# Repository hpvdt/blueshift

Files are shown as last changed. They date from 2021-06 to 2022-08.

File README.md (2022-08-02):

# Blueshift

Repository for our what would have been our 2020 ASME entry, Blueshift. Although the vehicle was never completed, the electronics were. The system is heavily based off of TITAN given they are both depend on a video system for the riders which is overlaid with vehicle data.

## Changes from TITAN

 However it has some changes from TITAN:
- Lighting hardware (and control) to meet road legality requirements
- Hardware was designed as an RPi HAT for a more compact system.
- Telemetry was operated by the microcontroller, not the RPi as on TITAN.
- Moved from a Python based overlay system to C based one to improve overlay update rate and prevent the overlay blacking out the video on occasion.

All systems were tested from home during the first set of lockdowns during COVID and were successful. So it is likely they would have worked just as well had the bike been built.

## Outcome

Work on this project ceased once the C-based overlay was working and telemetry was worked into it. Much of what was done for Blueshift will now go into improving TITAN for the future.

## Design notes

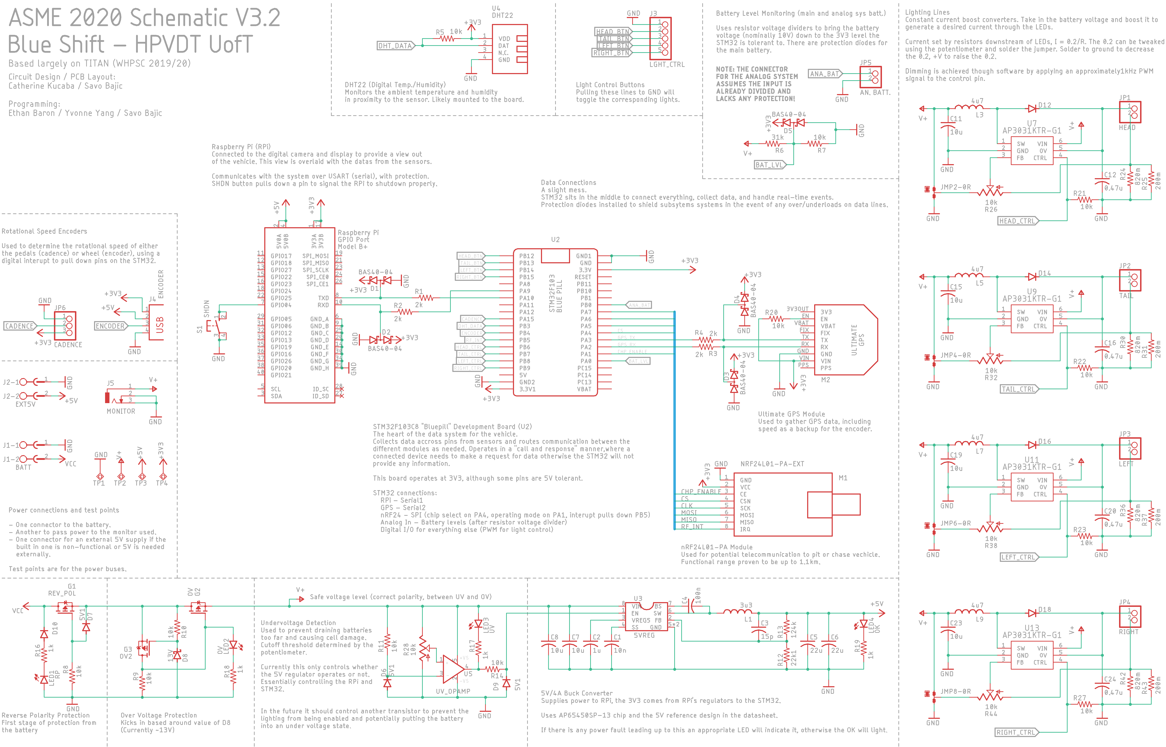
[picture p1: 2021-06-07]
Hardware/Schematic V3.2.png

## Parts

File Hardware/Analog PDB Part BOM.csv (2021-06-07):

Part | Value | Device | Package | Description
C1 | 10u | C-USC0603 | C0603 | CAPACITOR, American symbol
C2 | 4u7 | C-USC0603 | C0603 | CAPACITOR, American symbol
C3 | 2n2 | C-USC0603 | C0603 | CAPACITOR, American symbol
C4 | 10n | C-USC0603 | C0603 | CAPACITOR, American symbol
D1 | 0v2 | BOOSTDIODE | DO-214AB
H1 | MOUNT-HOLE3.3 | MOUNT-HOLE3.3 | 3,3 | MOUNTING HOLE with drill center marker
H2 | MOUNT-HOLE3.3 | MOUNT-HOLE3.3 | 3,3 | MOUNTING HOLE with drill center marker
L1 | 4u7 | SDEI054T | SDES053T | 4.7uH Inductor
R1 | 86k6 | R-US_R0402 | R0402 | RESISTOR, American symbol
R2 | 10k | R-US_R0402 | R0402 | RESISTOR, American symbol
R3 | 10k | R-US_R0402 | R0402 | RESISTOR, American symbol
R4 | 100k | R-US_R0402 | R0402 | RESISTOR, American symbol
R5 | 100k | R-US_R0402 | R0402 | RESISTOR, American symbol
U1 | MP3213DH | MP3213DH | 8-TSSOP | 3.5A Boost Converter Regulator
X1 | BATT | MST2V | MSTBV2 | PHOENIX
X2 | CAM1 | MSTBV2 | MSTBV2 | PHOENIX
X3 | CAM2 | MSTBV2 | MSTBV2 | PHOENIX
X4 | CAM3 | MSTBV2 | MSTBV2 | PHOENIX
X5 | DIS1 | MSTBV2 | MSTBV2 | PHOENIX
X6 | DIS2 | MSTBV2 | MSTBV2 | PHOENIX
X7 | DIS3 | MSTBV2 | MSTBV2 | PHOENIX

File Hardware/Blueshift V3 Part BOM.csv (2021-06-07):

Part | Value | Device | Package | Description
C1 | 10n | C-USC0402 | C0402 | CAPACITOR, American symbol
C2 | 1u | C-USC0402 | C0402 | CAPACITOR, American symbol
C3 | 15p | C-USC0402 | C0402 | CAPACITOR, American symbol
C4 | 100n | C-USC0402 | C0402 | CAPACITOR, American symbol
C5 | 22u | C-USC0805 | C0805 | CAPACITOR, American symbol
C6 | 22u | C-USC0805 | C0805 | CAPACITOR, American symbol
C7 | 10u | C-USC0805 | C0805 | CAPACITOR, American symbol
C8 | 10u | C-USC0805 | C0805 | CAPACITOR, American symbol
C11 | 10u | C-USC1206K | C1206K | CAPACITOR, American symbol
C12 | 0.47u | C-USC1206K | C1206K | CAPACITOR, American symbol
C15 | 10u | C-USC1206K | C1206K | CAPACITOR, American symbol
C16 | 0.47u | C-USC1206K | C1206K | CAPACITOR, American symbol
C19 | 10u | C-USC1206K | C1206K | CAPACITOR, American symbol
C20 | 0.47u | C-USC1206K | C1206K | CAPACITOR, American symbol
C23 | 10u | C-USC1206K | C1206K | CAPACITOR, American symbol
C24 | 0.47u | C-USC1206K | C1206K | CAPACITOR, American symbol
D1 | BAS40-04 | BAS40-04 | SOT23 | Silicon Schottky Diodes
D2 | BAS40-04 | BAS40-04 | SOT23 | Silicon Schottky Diodes
D3 | BAS40-04 | BAS40-04 | SOT23 | Silicon Schottky Diodes
D4 | BAS40-04 | BAS40-04 | SOT23 | Silicon Schottky Diodes
D5 | BAS40-04 | BAS40-04 | SOT23 | Silicon Schottky Diodes
D6 | 5V1 | DIODE-SOD323-R | SOD323-R | DIODE
D7 | 5V1 | DIODE-SOD323-R | SOD323-R | DIODE
D8 | 13V | BAS70 | SOT23 | Silicon Schottky Diodes
D9 | 5V1 | DIODE-SOD323-R | SOD323-R | DIODE
D10 |  | DIODE-SOD80C | SOD80C | DIODE
D12 |  | DIODE-DO-214AC | DO-214AC | DIODE
D14 |  | DIODE-DO-214AC | DO-214AC | DIODE
D16 |  | DIODE-DO-214AC | DO-214AC | DIODE
D18 |  | DIODE-DO-214AC | DO-214AC | DIODE
G1 | REV_POL | SI3493DDV-T1-GE3 | TSOP-6 | 20V P-CH MOSFET
G2 | OV | SI3493DDV-T1-GE3 | TSOP-6 | 20V P-CH MOSFET
G3 | OV2 | SI3493DDV-T1-GE3 | TSOP-6 | 20V P-CH MOSFET
J1 | BATT | MST2V | MSTBV2 | PHOENIX
J2 | EXT5V | MST2V | MSTBV2 | PHOENIX
J3 | LGHT_CTRL | PINHD-1X5 | 1X05 | PIN HEADER
J4 | ENCODER | PN87520 | PN87520 | BERG USB connector
J5 | MONITOR | DCJ0303 | DCJ0303 | DC POWER JACK
JMP2 | 0R-JUMPA | 0R-JUMPA | A0R-JMP | SMD 0R 0805 Jumper
JMP4 | 0R-JUMPA | 0R-JUMPA | A0R-JMP | SMD 0R 0805 Jumper
JMP6 | 0R-JUMPA | 0R-JUMPA | A0R-JMP | SMD 0R 0805 Jumper
JMP8 | 0R-JUMPA | 0R-JUMPA | A0R-JMP | SMD 0R 0805 Jumper
JP1 | HEAD | PINHD-1X2 | 1X02 | PIN HEADER
JP2 | TAIL | PINHD-1X2 | 1X02 | PIN HEADER
JP3 | LEFT | PINHD-1X2 | 1X02 | PIN HEADER
JP4 | RIGHT | PINHD-1X2 | 1X02 | PIN HEADER
JP5 | AN. BATT. | PINHD-1X2 | 1X02 | PIN HEADER
JP6 | CADENCE | PINHD-1X3 | 1X03 | PIN HEADER
L1 | 3u3 | SDES064T-3R3MS | SDES064T
L3 | 4u7 | NR6028NR6028 | INDDFN600X600X280-2N
L5 | 4u7 | NR6028NR6028 | INDDFN600X600X280-2N
L7 | 4u7 | NR6028NR6028 | INDDFN600X600X280-2N
L9 | 4u7 | NR6028NR6028 | INDDFN600X600X280-2N
LED1 | RP | LEDSML0805 | SML0805 | LED
LED2 | OV | LEDSML0805 | SML0805 | LED
LED3 | UV | LEDSML0805 | SML0805 | LED
LED4 | OK | LEDSML0805 | SML0805 | LED
M1 | NRF24L01-PA-EXT | WIRELESS-NRF24L01-PA-EXT | WIRELESS-NRF24L01-PA-EXT | 2.4 GHz Wireless Module based on NRF24L01 chip with preamplifier and external antenna
M2 | ULTIMATE-GPS | ULTIMATE-GPS | ULTIMATE_GPS
R1 | 2k | R-US_R0402 | R0402 | RESISTOR, American symbol
R2 | 2k | R-US_R0402 | R0402 | RESISTOR, American symbol
R3 | 2k | R-US_R0402 | R0402 | RESISTOR, American symbol
R4 | 2k | R-US_R0402 | R0402 | RESISTOR, American symbol
R5 | 10k | R-US_R0402 | R0402 | RESISTOR, American symbol
R6 | 31k | R-US_R0402 | R0402 | RESISTOR, American symbol
R7 | 10k | R-US_R0402 | R0402 | RESISTOR, American symbol
R8 | 10k | R-US_R0402 | R0402 | RESISTOR, American symbol
R9 | 10k | R-US_R0402 | R0402 | RESISTOR, American symbol
R10 | 10k | R-US_R0402 | R0402 | RESISTOR, American symbol
R11 | 10k | R-US_R0402 | R0402 | RESISTOR, American symbol
R12 | 22k1 | R-US_R0402 | R0402 | RESISTOR, American symbol
R13 | 124k | R-US_R0402 | R0402 | RESISTOR, American symbol
R14 | 10k | R-US_R0402 | R0402 | RESISTOR, American symbol
R16 | 1k | R-US_R0402 | R0402 | RESISTOR, American symbol
R17 | 1k | R-US_R0402 | R0402 | RESISTOR, American symbol
R18 | 1k | R-US_R0402 | R0402 | RESISTOR, American symbol
R19 | 1k | R-US_R0402 | R0402 | RESISTOR, American symbol
R20 | 10k | R-US_R0402 | R0402 | RESISTOR, American symbol
R21 | 10k | R-US_R0402 | R0402 | RESISTOR, American symbol
R22 | 10k | R-US_R0402 | R0402 | RESISTOR, American symbol
R23 | 10k | R-US_R0402 | R0402 | RESISTOR, American symbol
R24 | 820m | R-US_R0603 | R0603 | RESISTOR, American symbol
R25 | 200m | R-US_R0805 | R0805 | RESISTOR, American symbol
R26 | 10k | TRIM_US-RJ9W | RJ9W | POTENTIOMETER
R27 | 10k | R-US_R0402 | R0402 | RESISTOR, American symbol
R28 | 10k | TRIM_US-RJ9W | RJ9W | POTENTIOMETER
R30 | 820m | R-US_R0603 | R0603 | RESISTOR, American symbol
R31 | 200m | R-US_R0805 | R0805 | RESISTOR, American symbol
R32 | 10k | TRIM_US-RJ9W | RJ9W | POTENTIOMETER
R36 | 820m | R-US_R0603 | R0603 | RESISTOR, American symbol
R37 | 200m | R-US_R0805 | R0805 | RESISTOR, American symbol
R38 | 10k | TRIM_US-RJ9W | RJ9W | POTENTIOMETER
R42 | 820m | R-US_R0603 | R0603 | RESISTOR, American symbol
R43 | 200m | R-US_R0805 | R0805 | RESISTOR, American symbol
R44 | 10k | TRIM_US-RJ9W | RJ9W | POTENTIOMETER
S1 | SHDN | 10-XX | B3F-10XX | OMRON SWITCH
TP1 | TPSQTP20SQ | TPSQTP20SQ | TP20SQ | Test pad
TP2 | TPSQTP20R | TPSQTP20R | TP20R | Test pad
TP3 | TPSQTP20R | TPSQTP20R | TP20R | Test pad
TP4 | TPSQTP20R | TPSQTP20R | TP20R | Test pad
U1 | RASPI_HAT | RASPI_HAT | RASPI_BOARD_B+HAT_CF
U2 | BLUEPILL | BLUE_PILL | BLUE_PILL
U3 | 5VREG | AP65450SP-13 | SO-8EP | AP65450
U4 | DHT22 | TEMP-HUM-SENSOR-DHT22 | TEMP-HUM-SENSOR-DHT22 | DHT22 - digital humidity & temperature sensor
U5 | UV_OPAMP | TA75S558F,LF | SOT-753
U7 | AP3031KTR-G1 | AP3031KTR-G1 | SOT23-6 | AP3031 step-up LED driver chip for LEDs up to 1.4A
U9 | AP3031KTR-G1 | AP3031KTR-G1 | SOT23-6 | AP3031 step-up LED driver chip for LEDs up to 1.4A
U11 | AP3031KTR-G1 | AP3031KTR-G1 | SOT23-6 | AP3031 step-up LED driver chip for LEDs up to 1.4A
U13 | AP3031KTR-G1 | AP3031KTR-G1 | SOT23-6 | AP3031 step-up LED driver chip for LEDs up to 1.4A

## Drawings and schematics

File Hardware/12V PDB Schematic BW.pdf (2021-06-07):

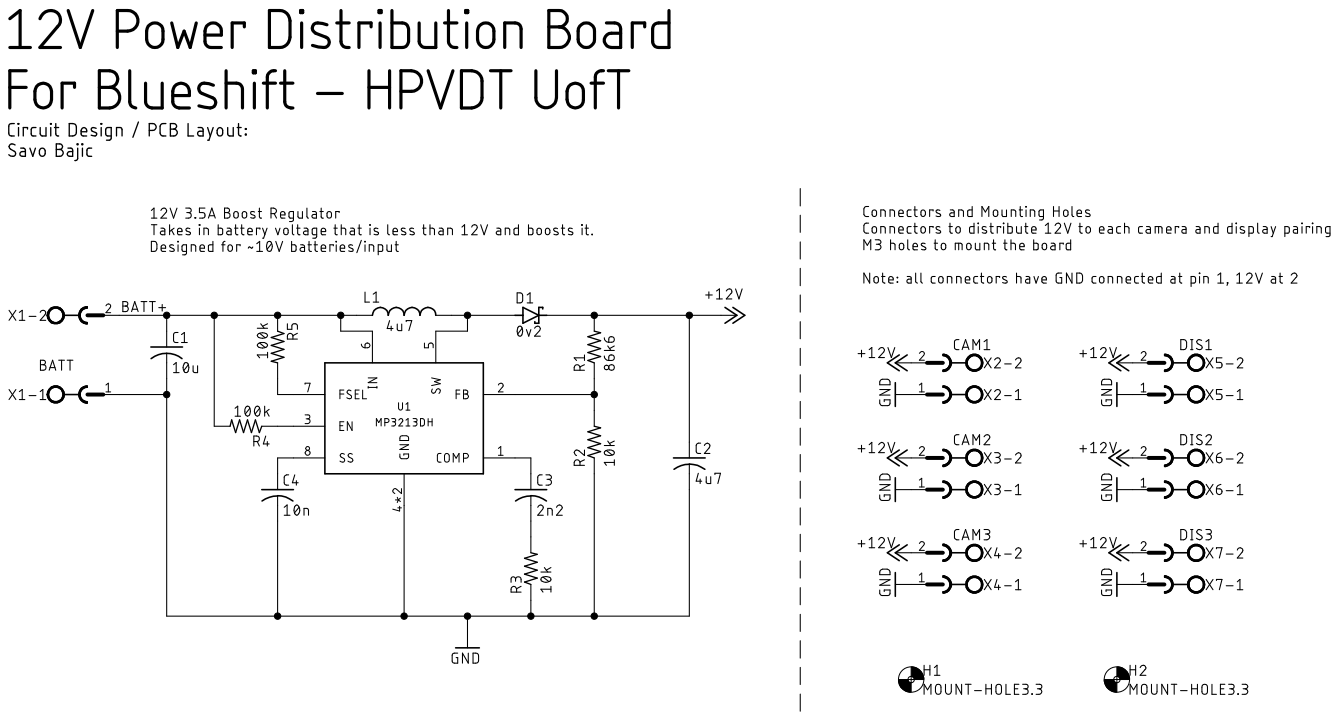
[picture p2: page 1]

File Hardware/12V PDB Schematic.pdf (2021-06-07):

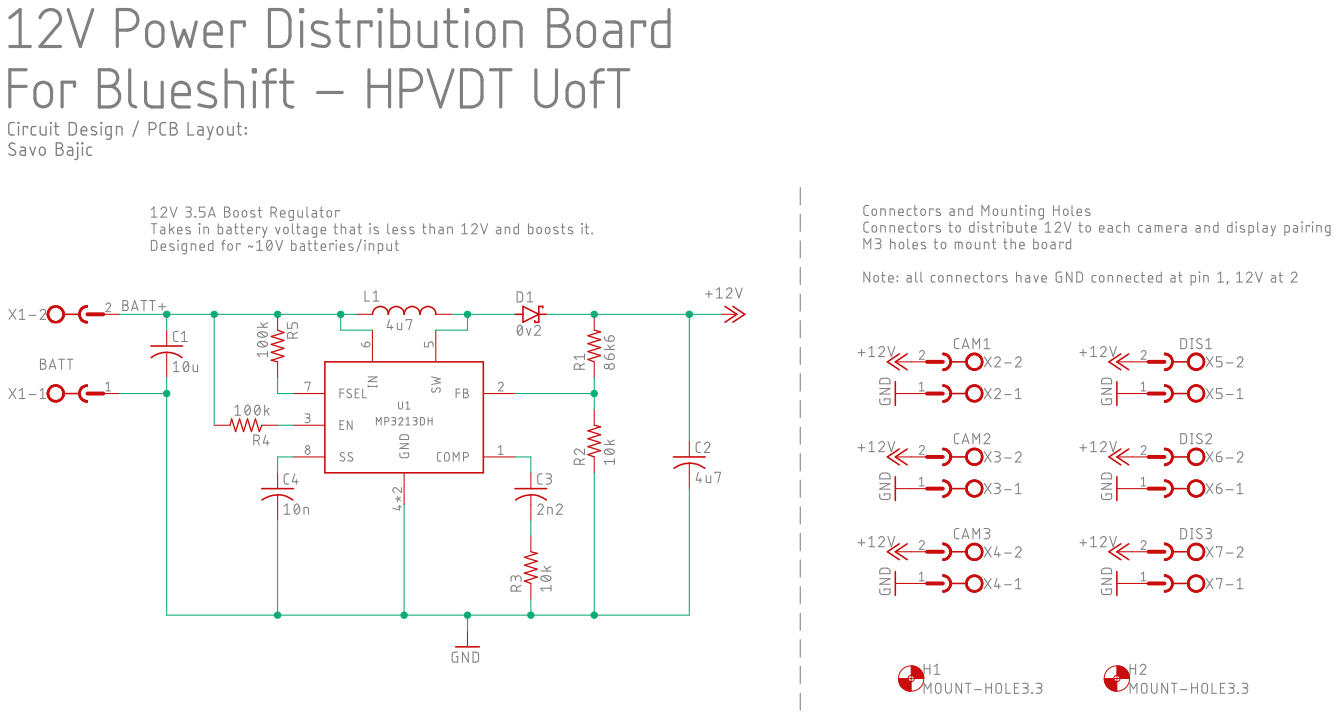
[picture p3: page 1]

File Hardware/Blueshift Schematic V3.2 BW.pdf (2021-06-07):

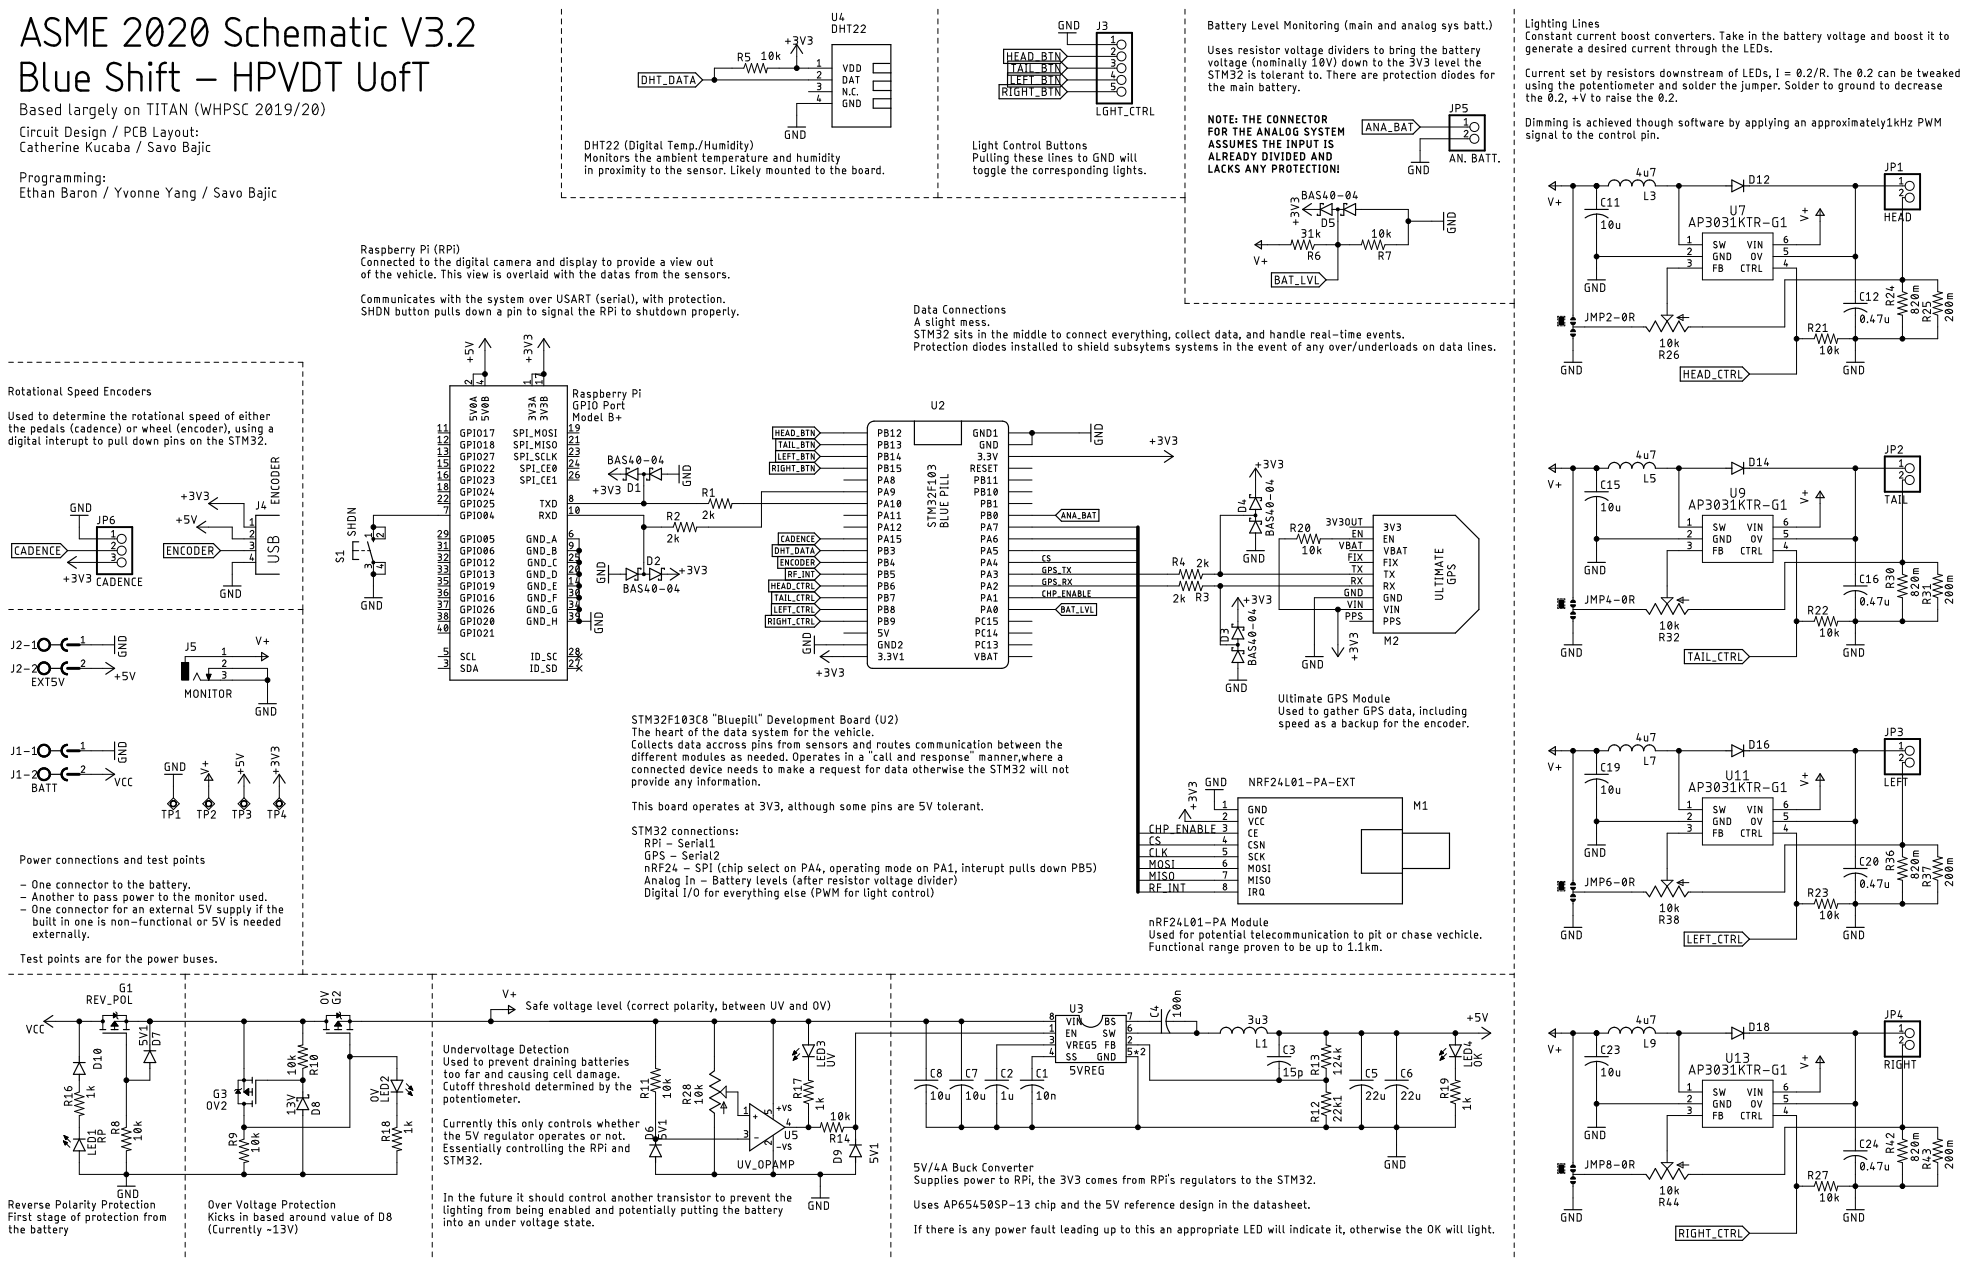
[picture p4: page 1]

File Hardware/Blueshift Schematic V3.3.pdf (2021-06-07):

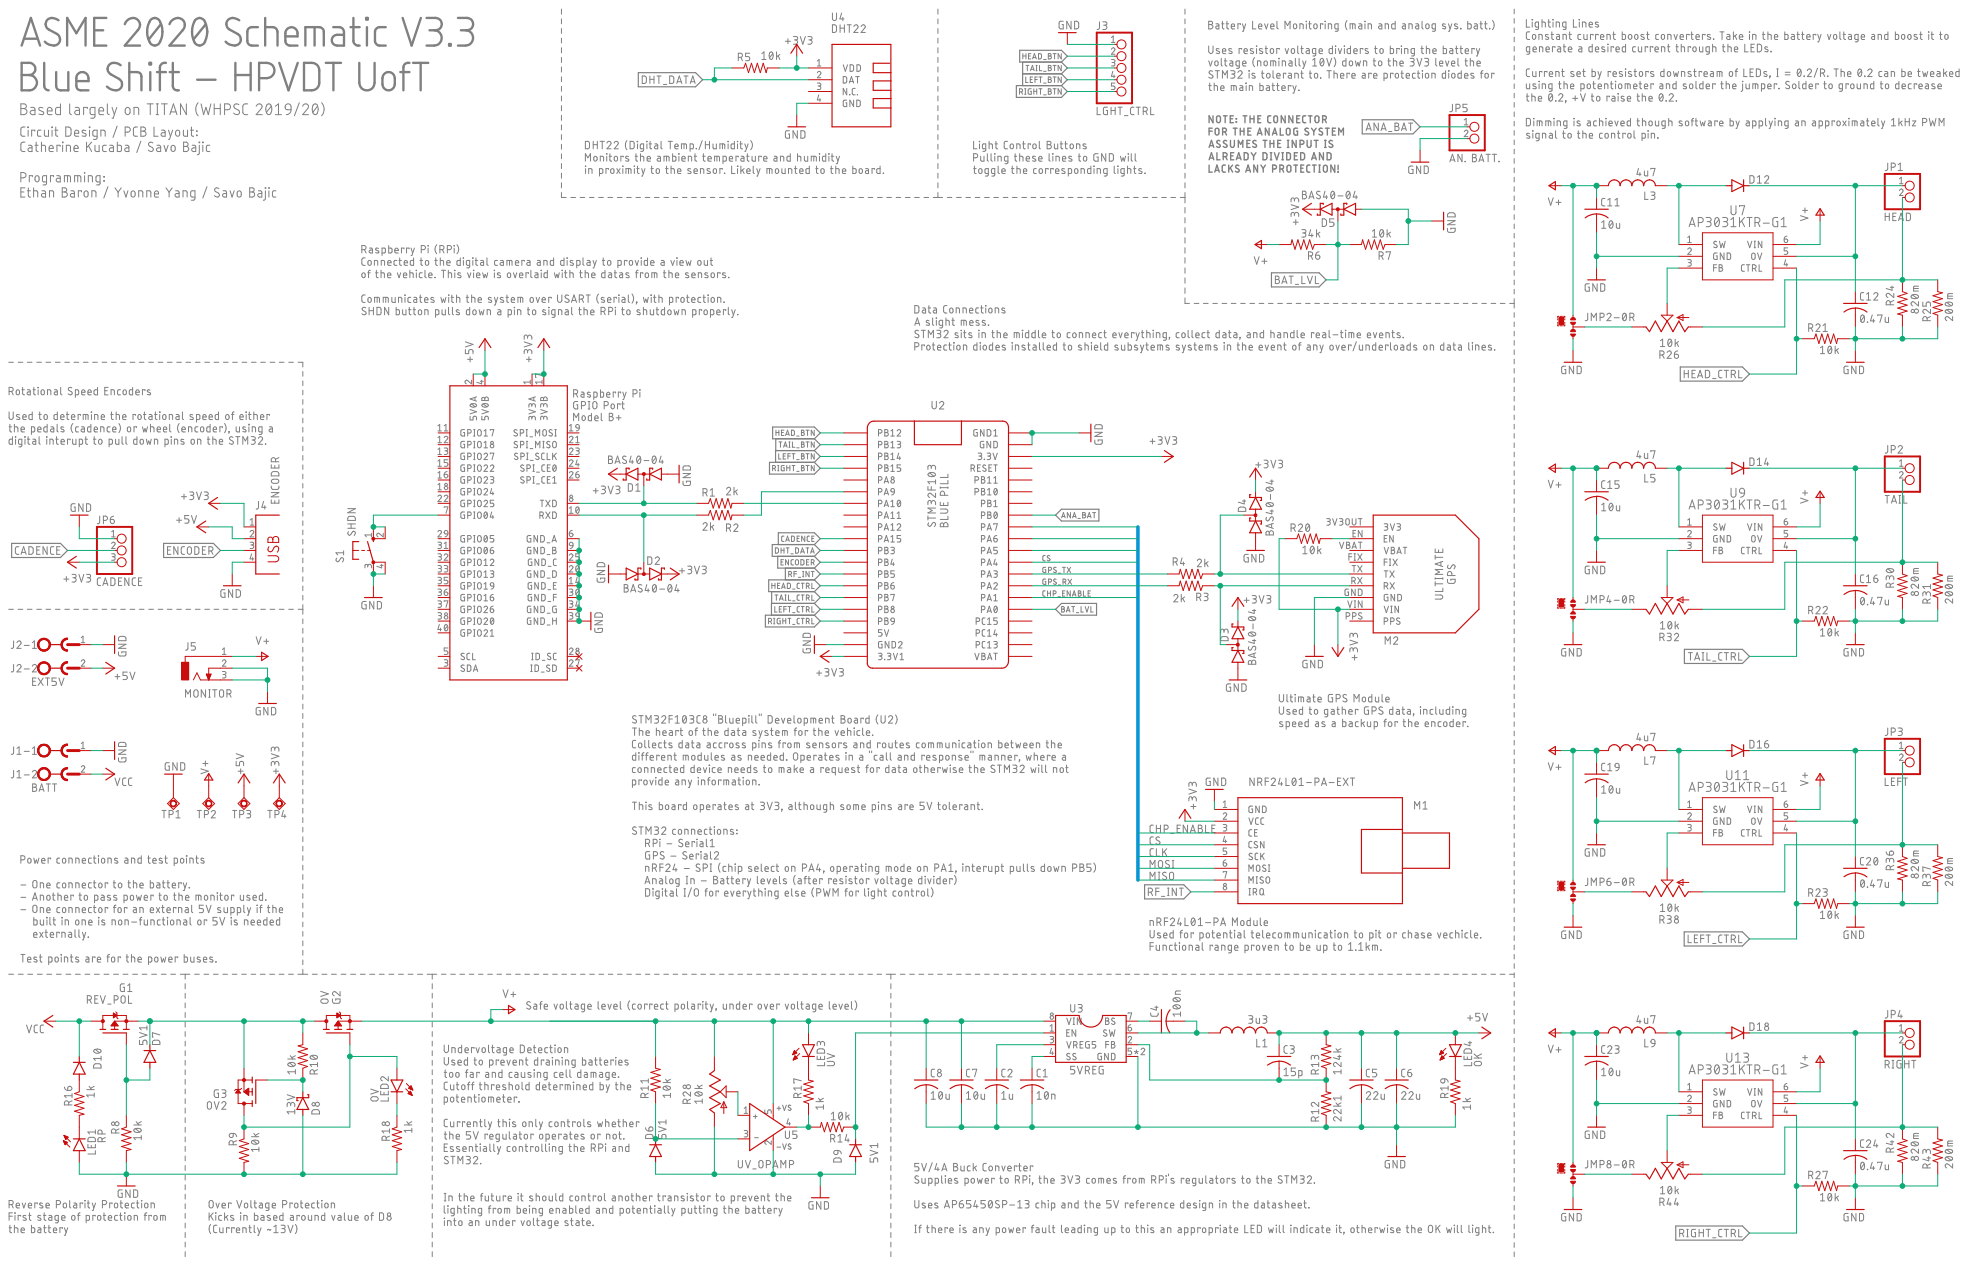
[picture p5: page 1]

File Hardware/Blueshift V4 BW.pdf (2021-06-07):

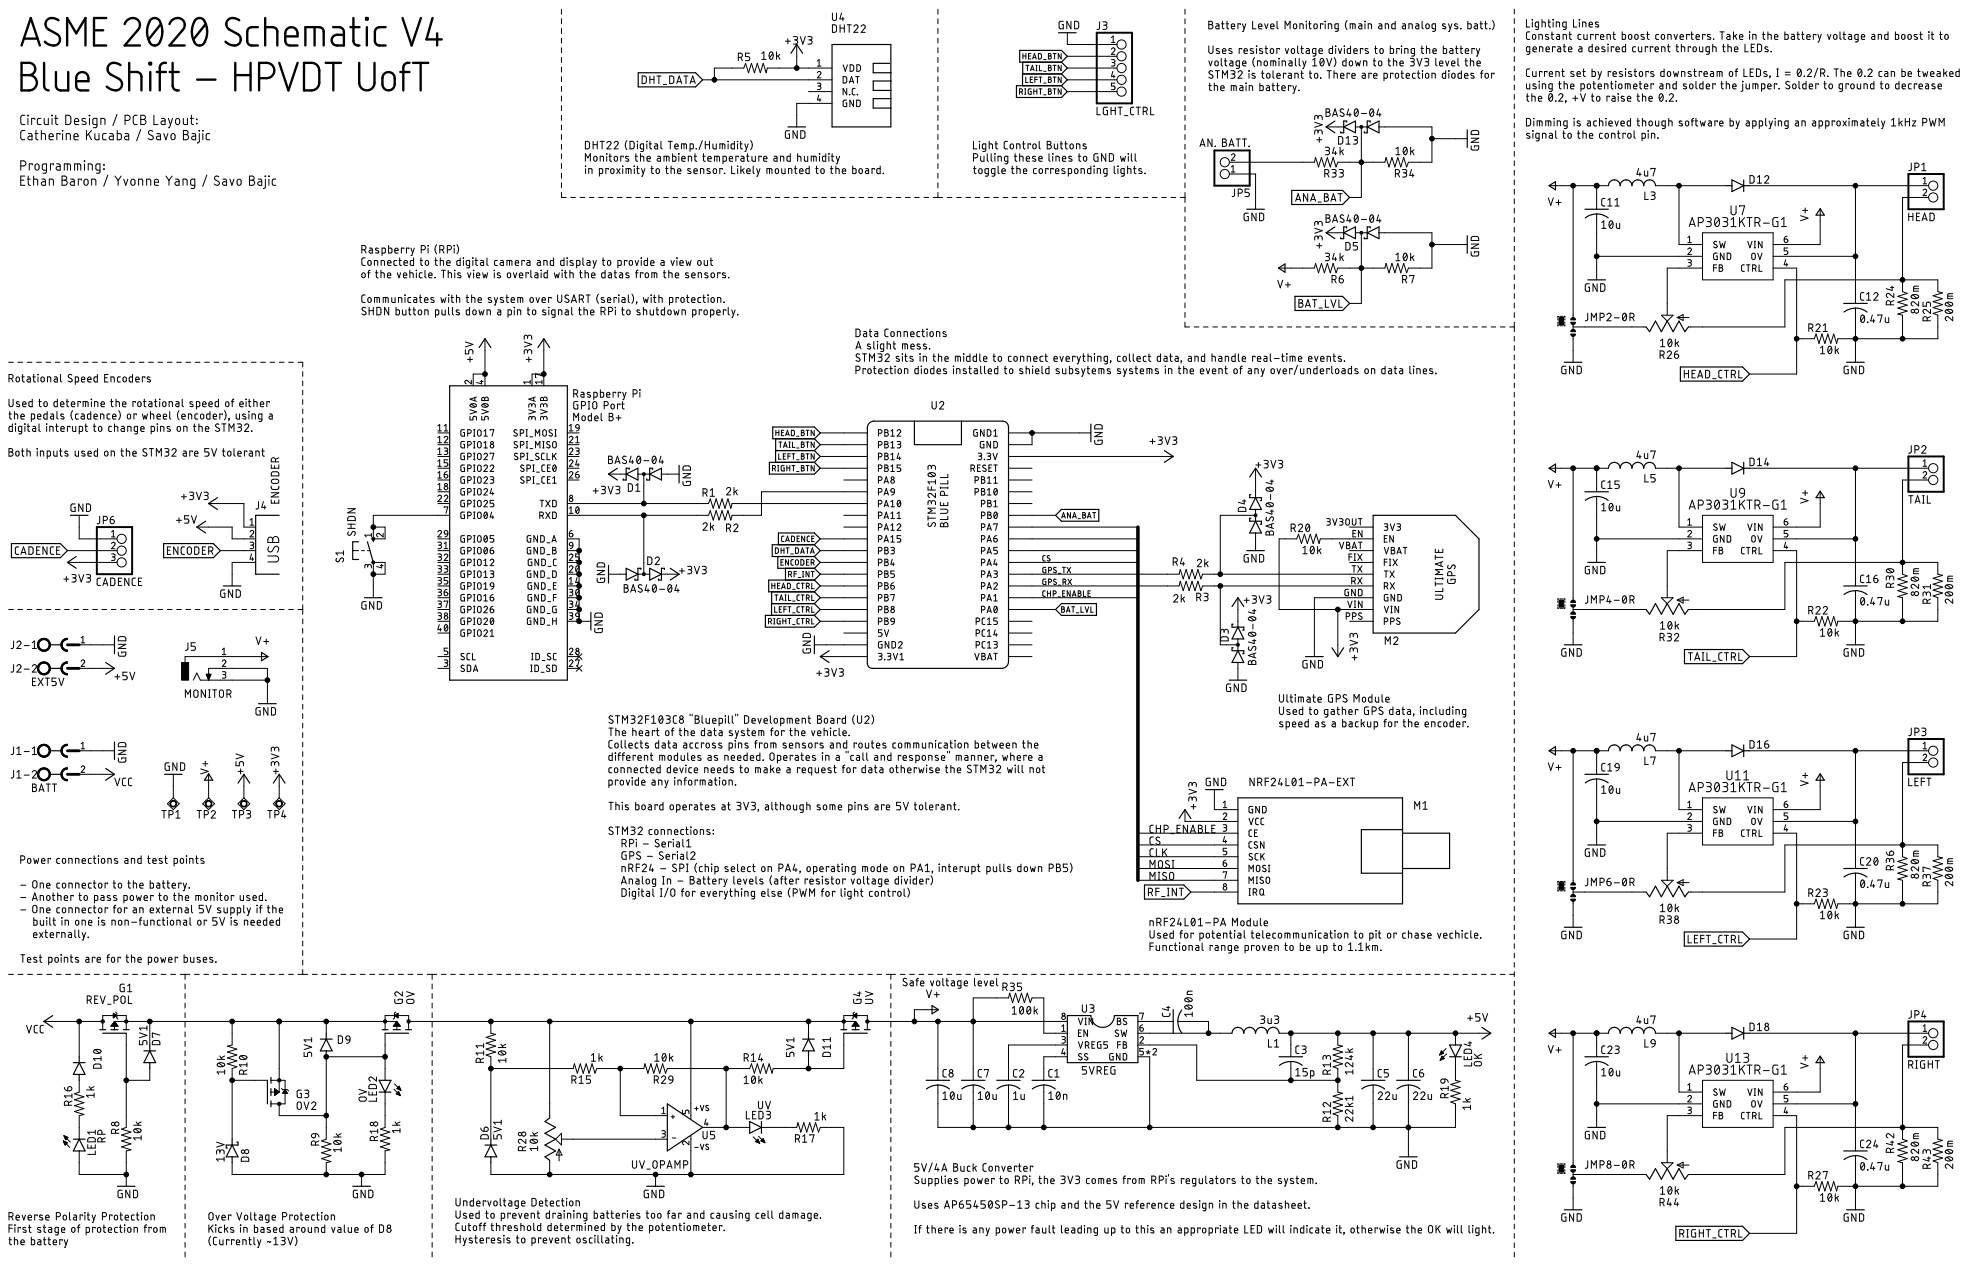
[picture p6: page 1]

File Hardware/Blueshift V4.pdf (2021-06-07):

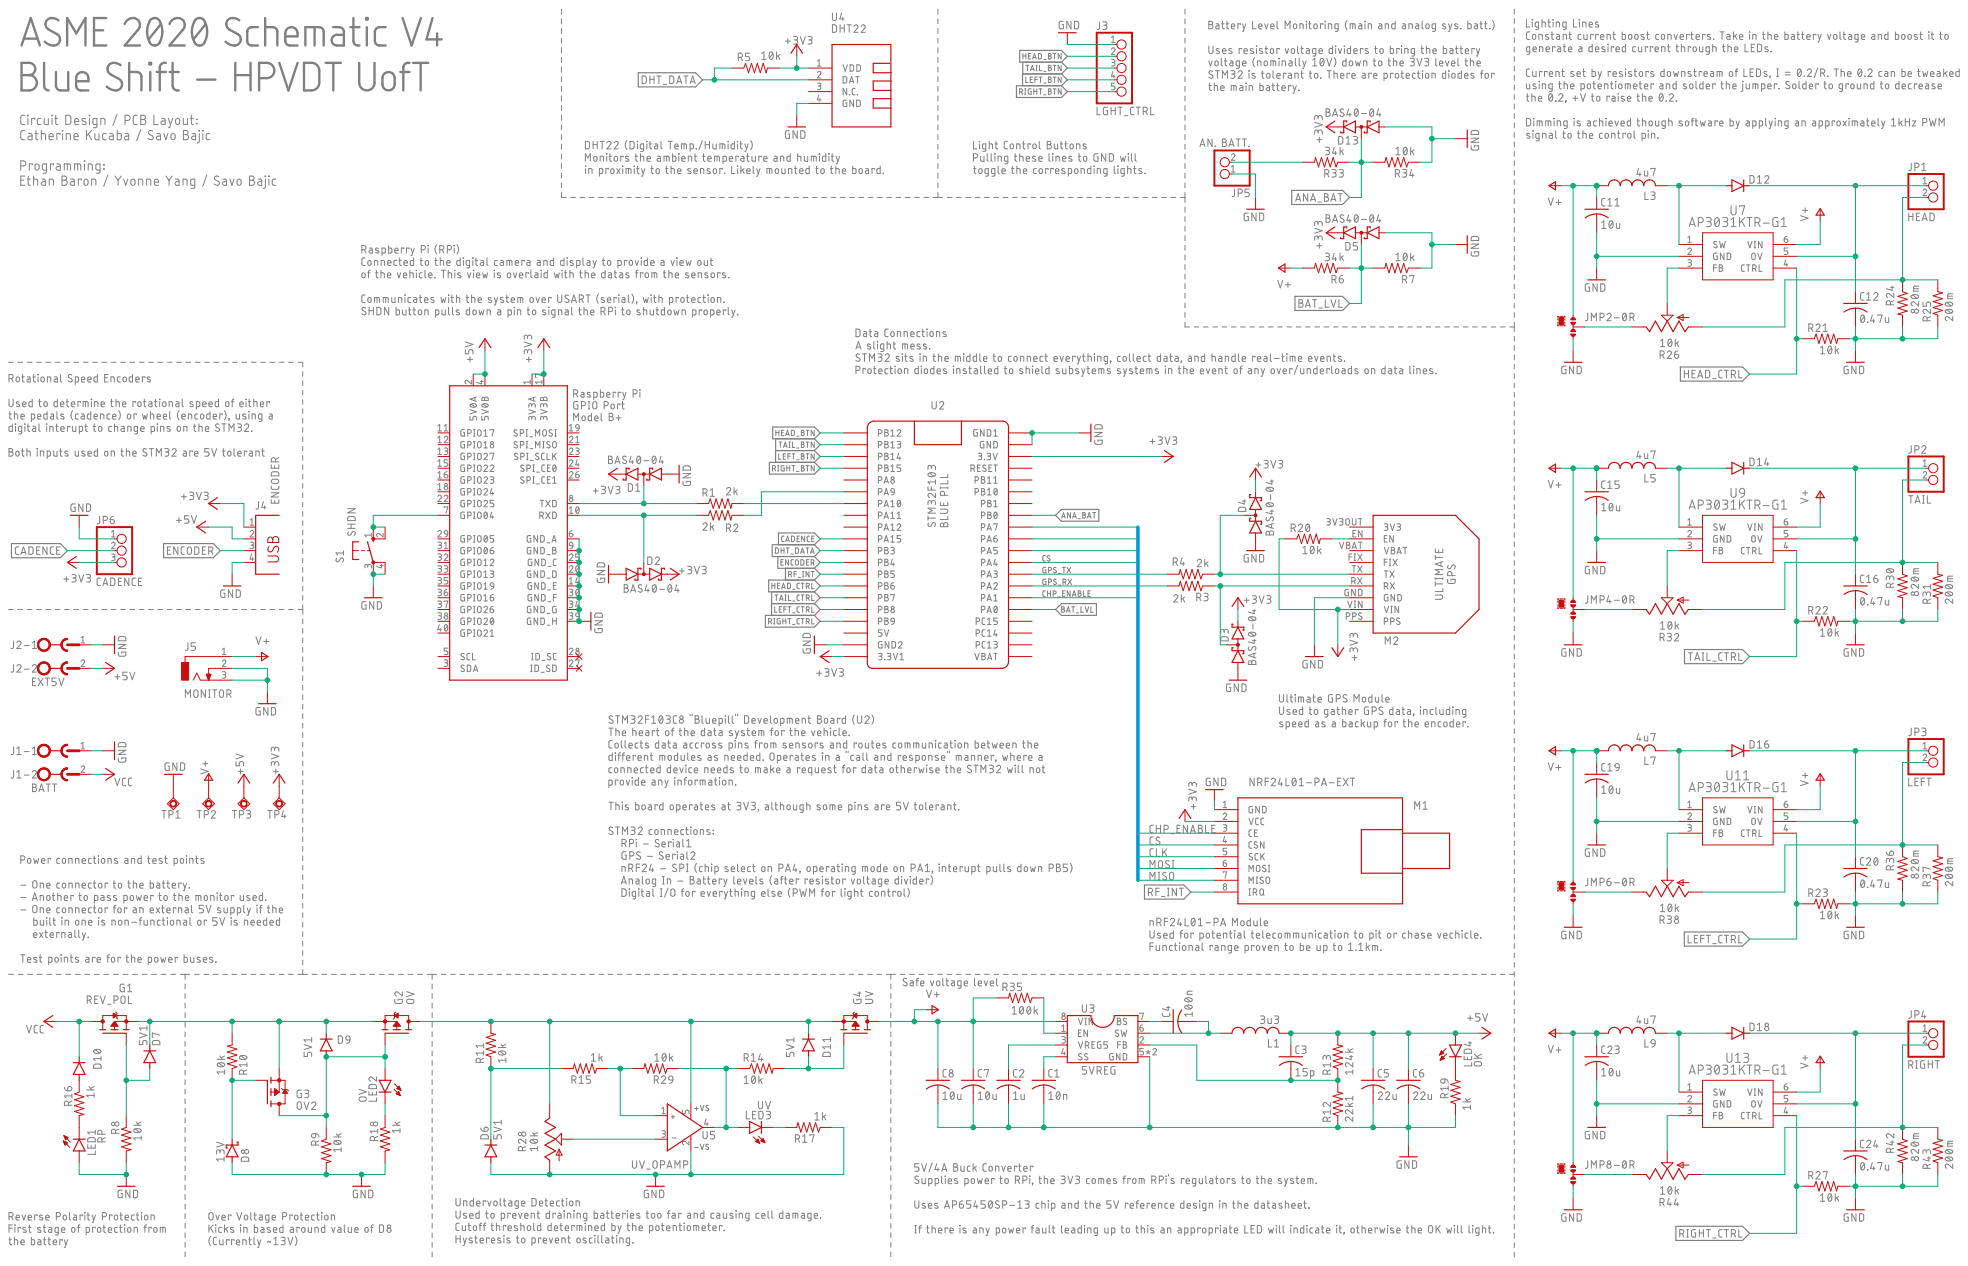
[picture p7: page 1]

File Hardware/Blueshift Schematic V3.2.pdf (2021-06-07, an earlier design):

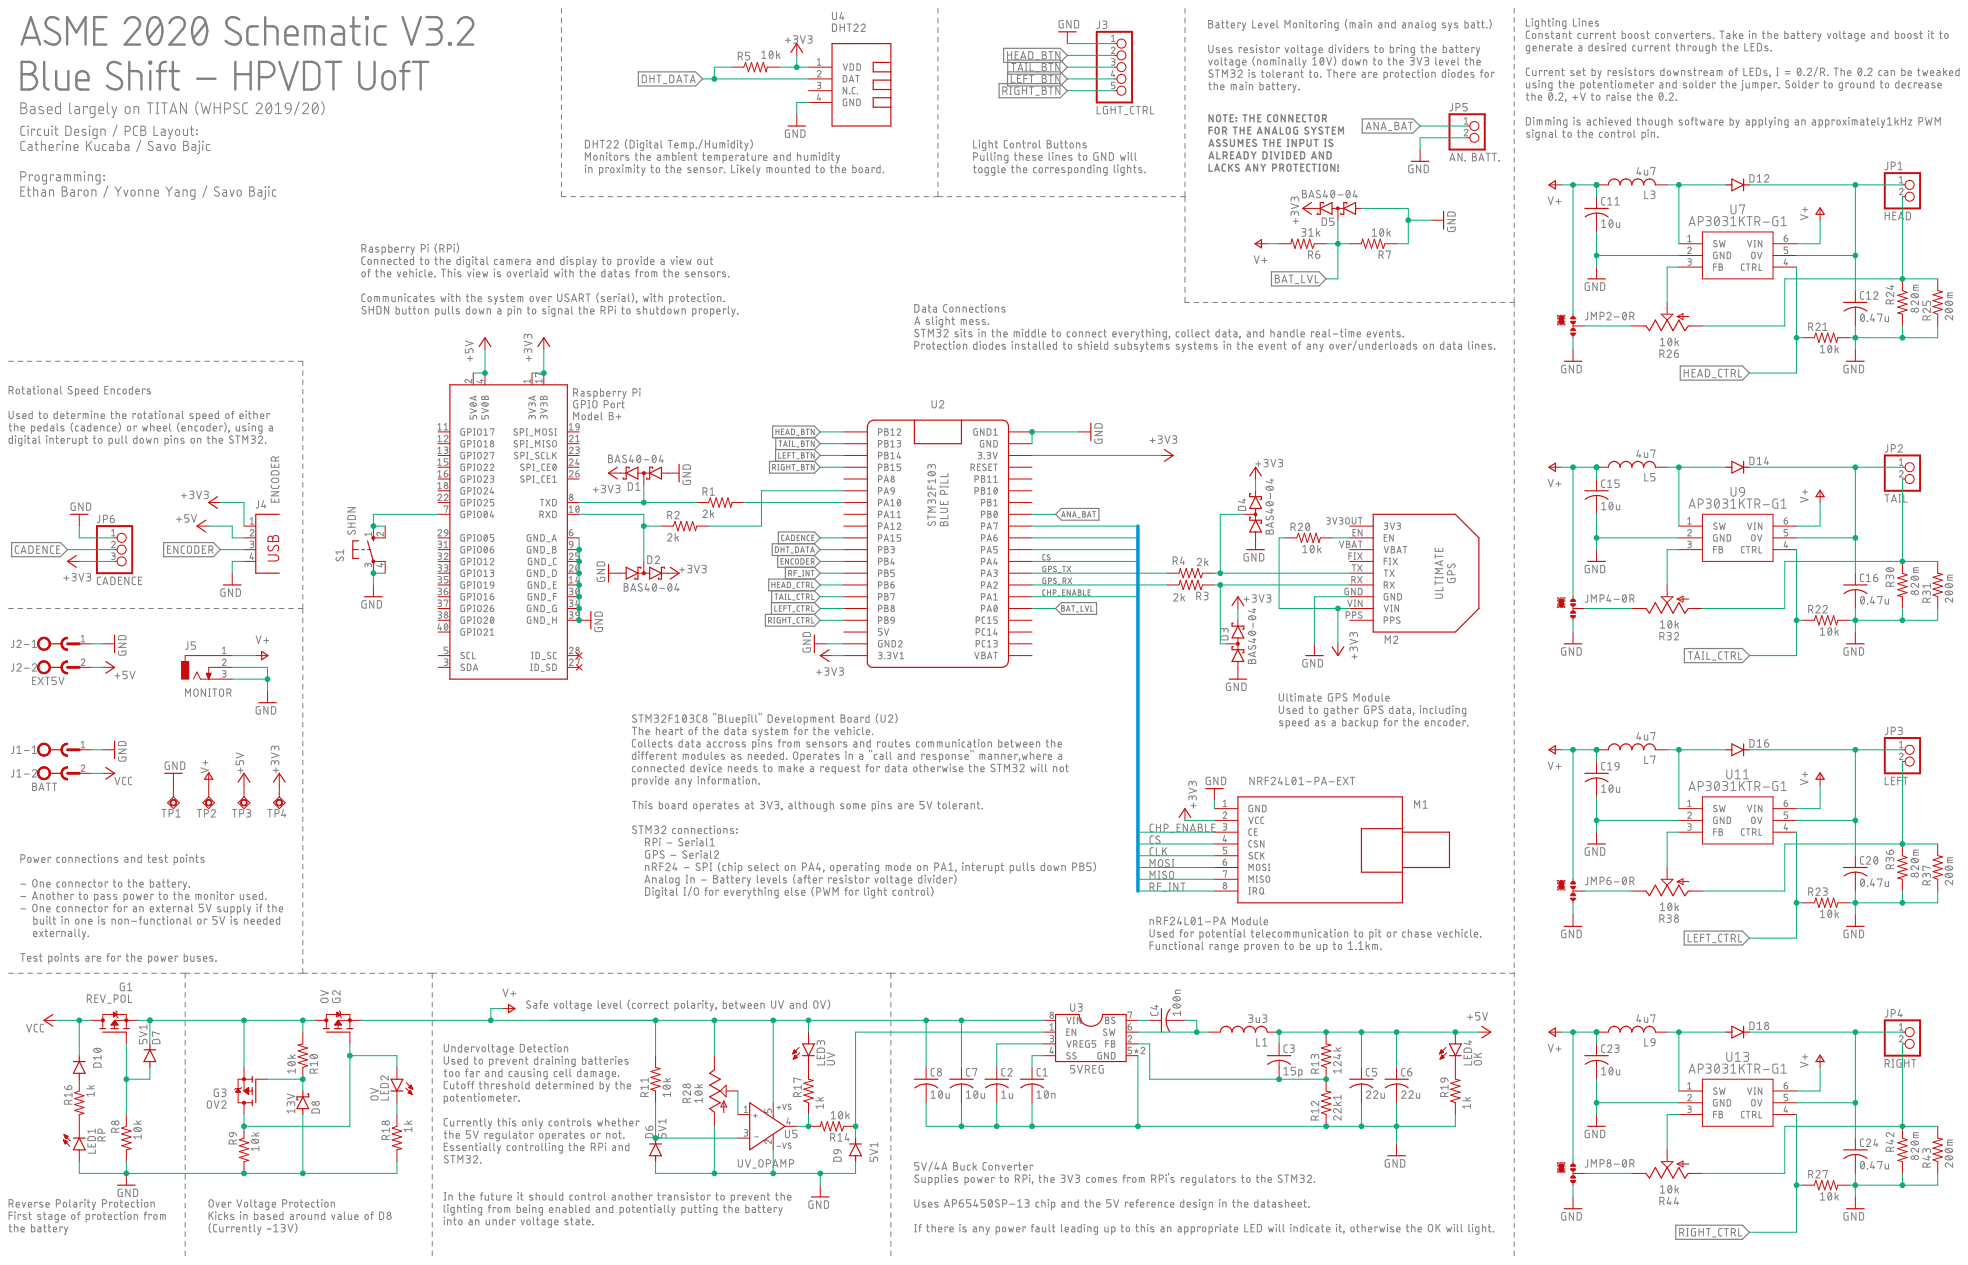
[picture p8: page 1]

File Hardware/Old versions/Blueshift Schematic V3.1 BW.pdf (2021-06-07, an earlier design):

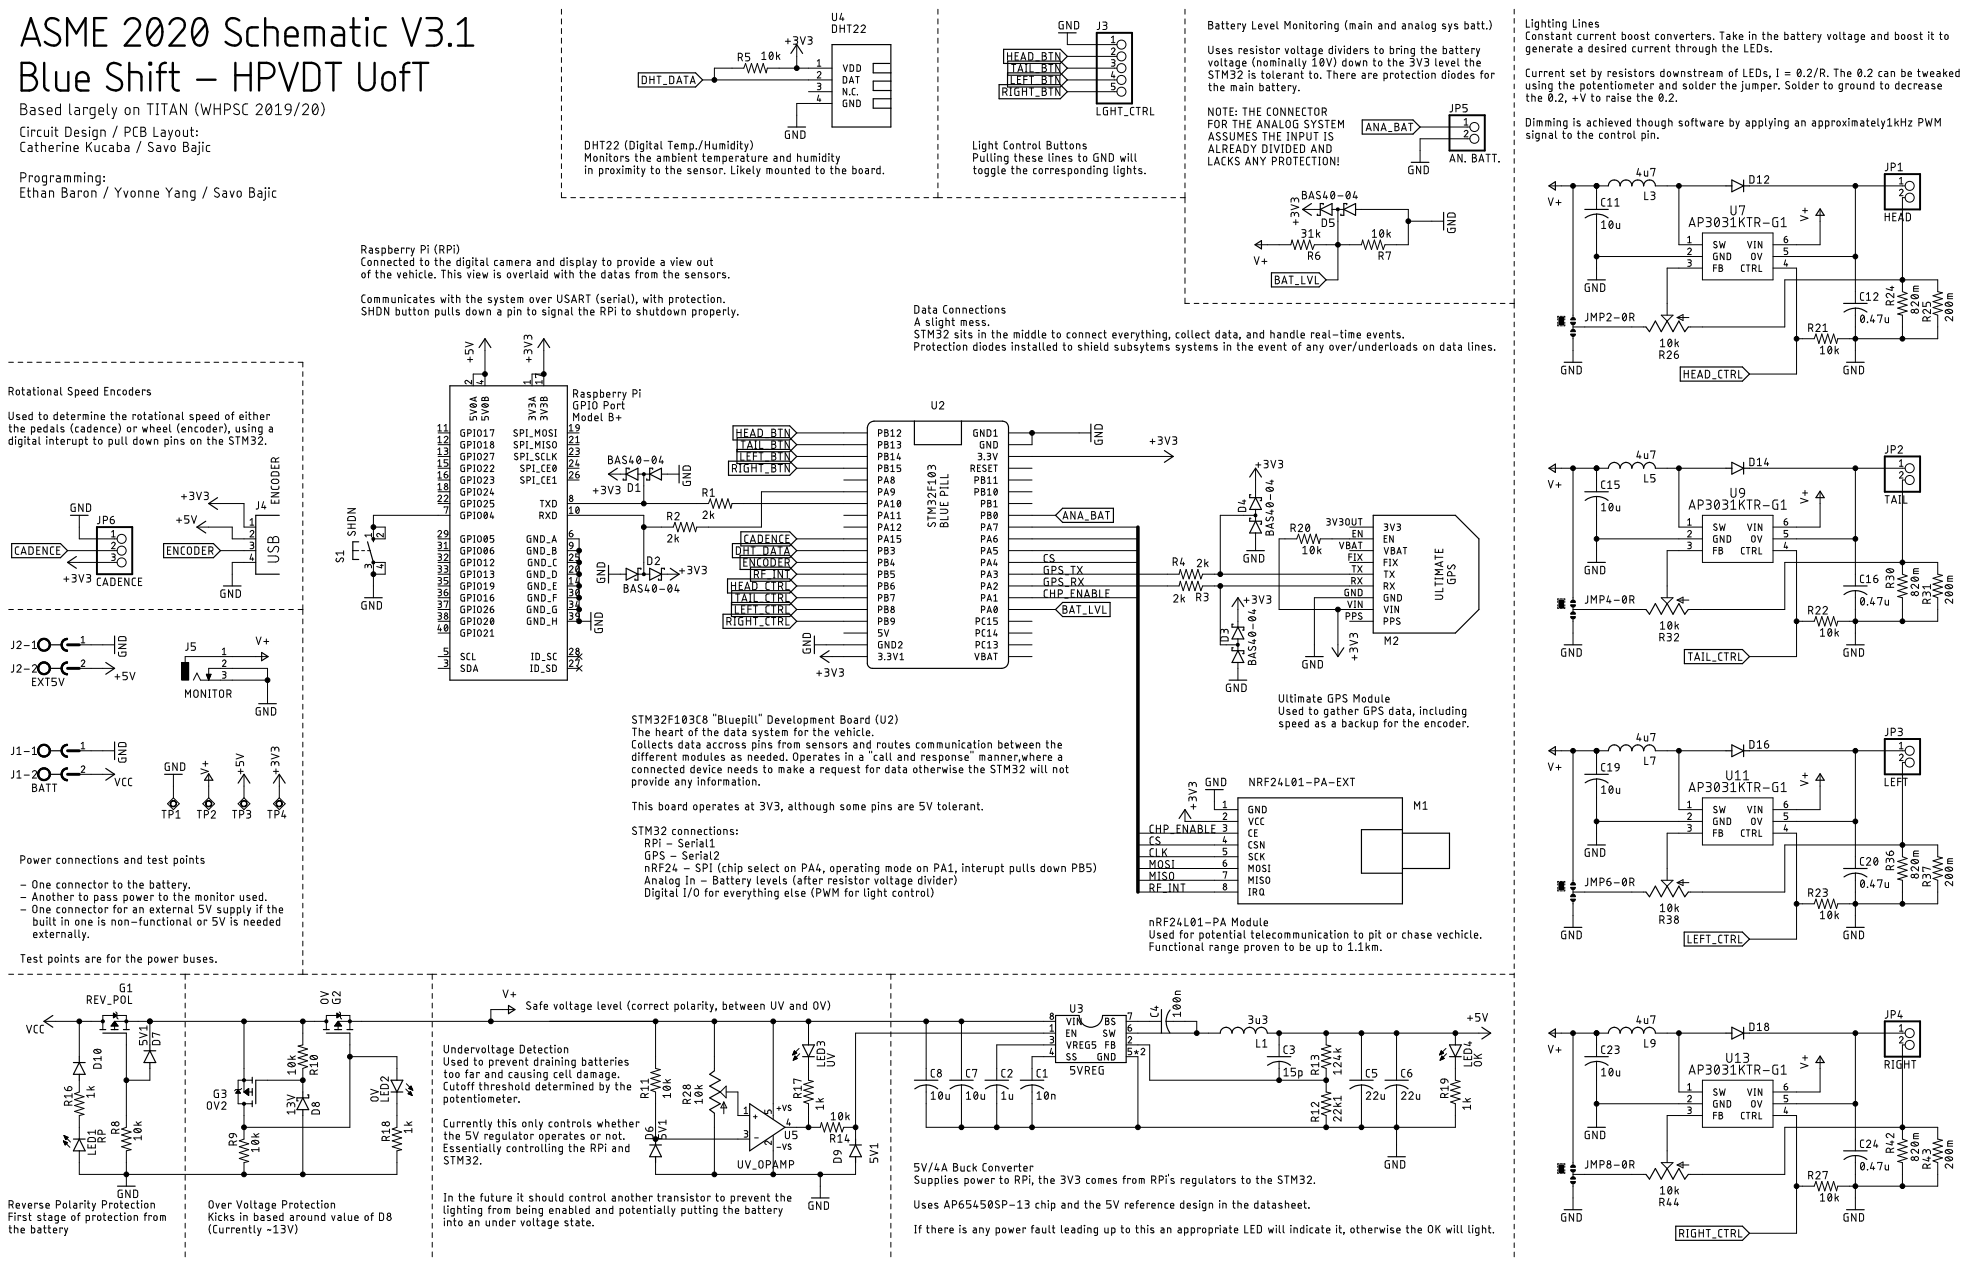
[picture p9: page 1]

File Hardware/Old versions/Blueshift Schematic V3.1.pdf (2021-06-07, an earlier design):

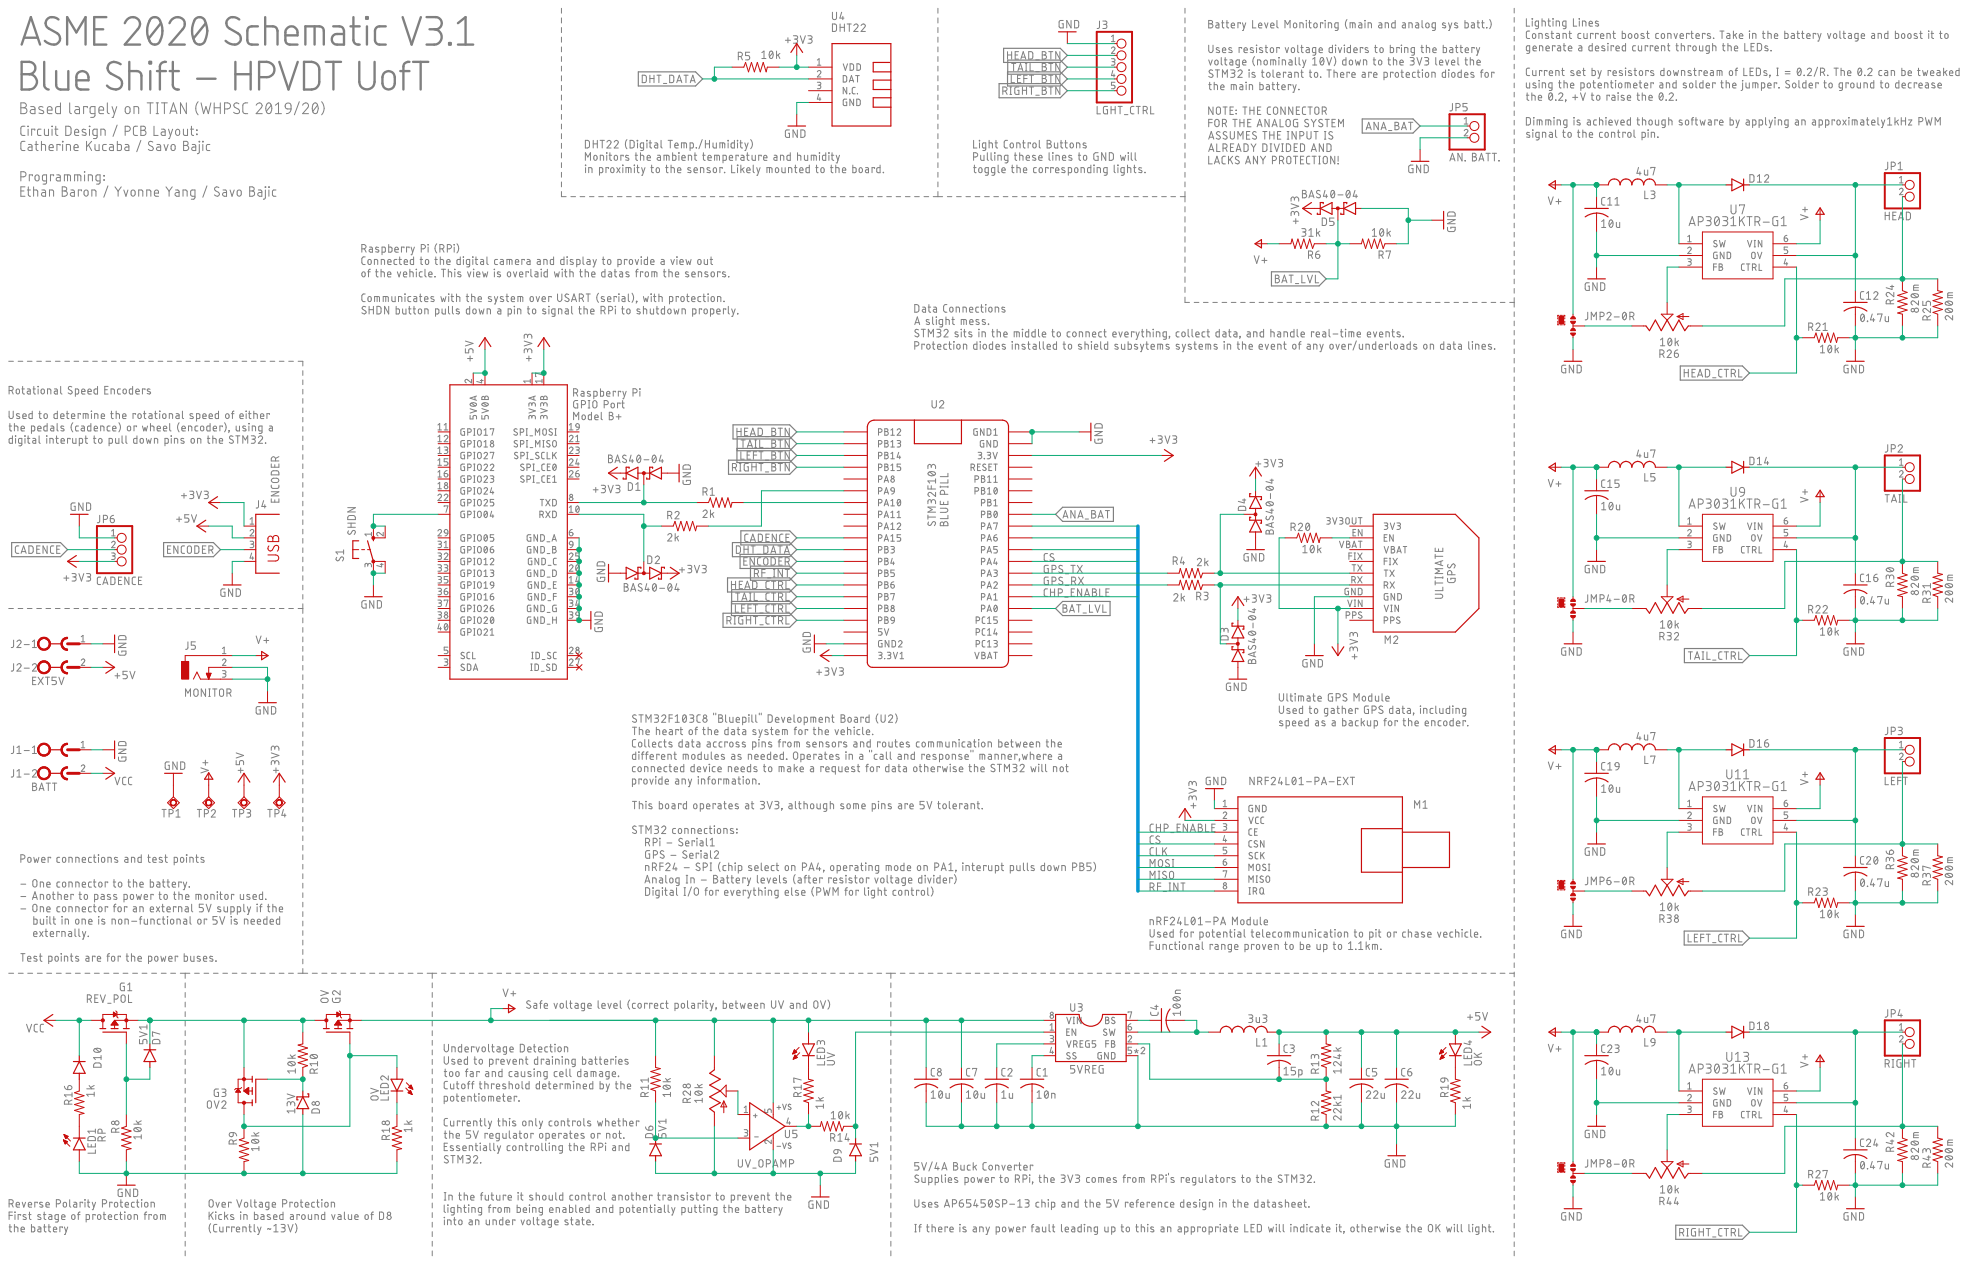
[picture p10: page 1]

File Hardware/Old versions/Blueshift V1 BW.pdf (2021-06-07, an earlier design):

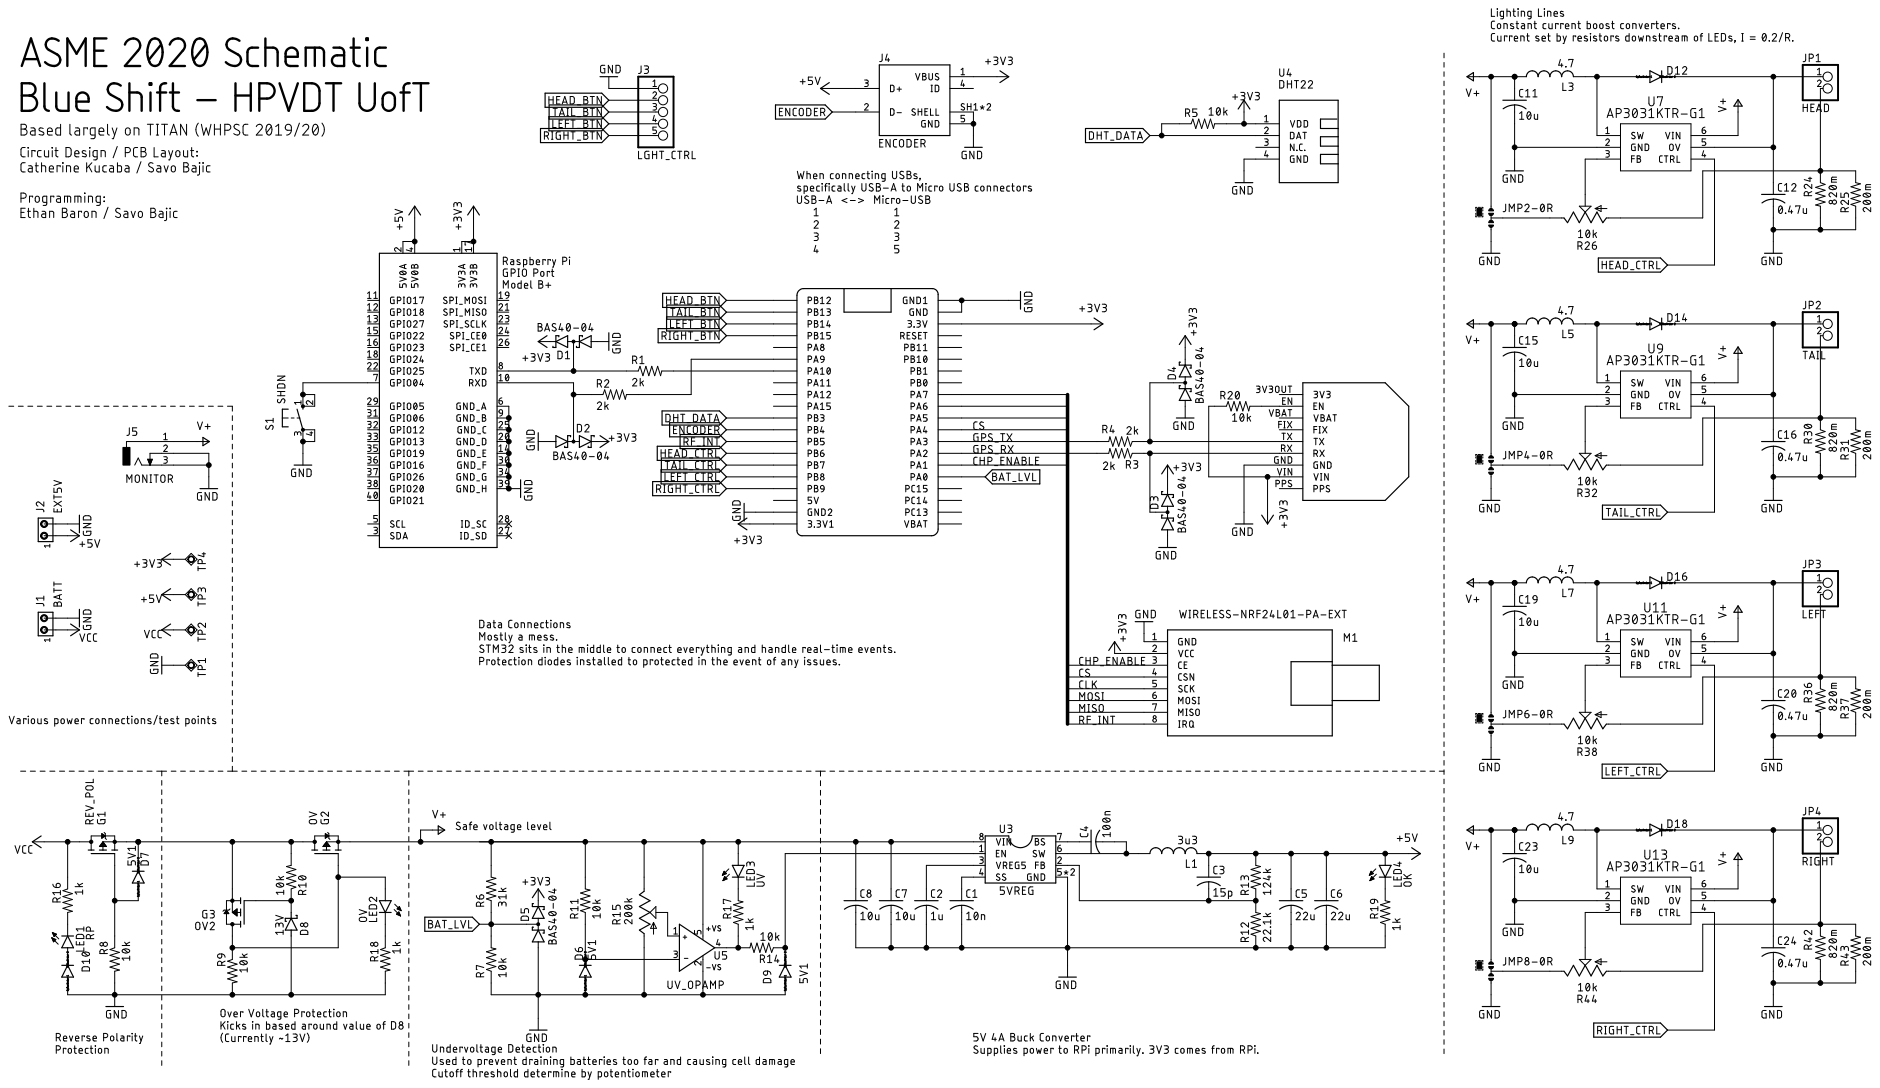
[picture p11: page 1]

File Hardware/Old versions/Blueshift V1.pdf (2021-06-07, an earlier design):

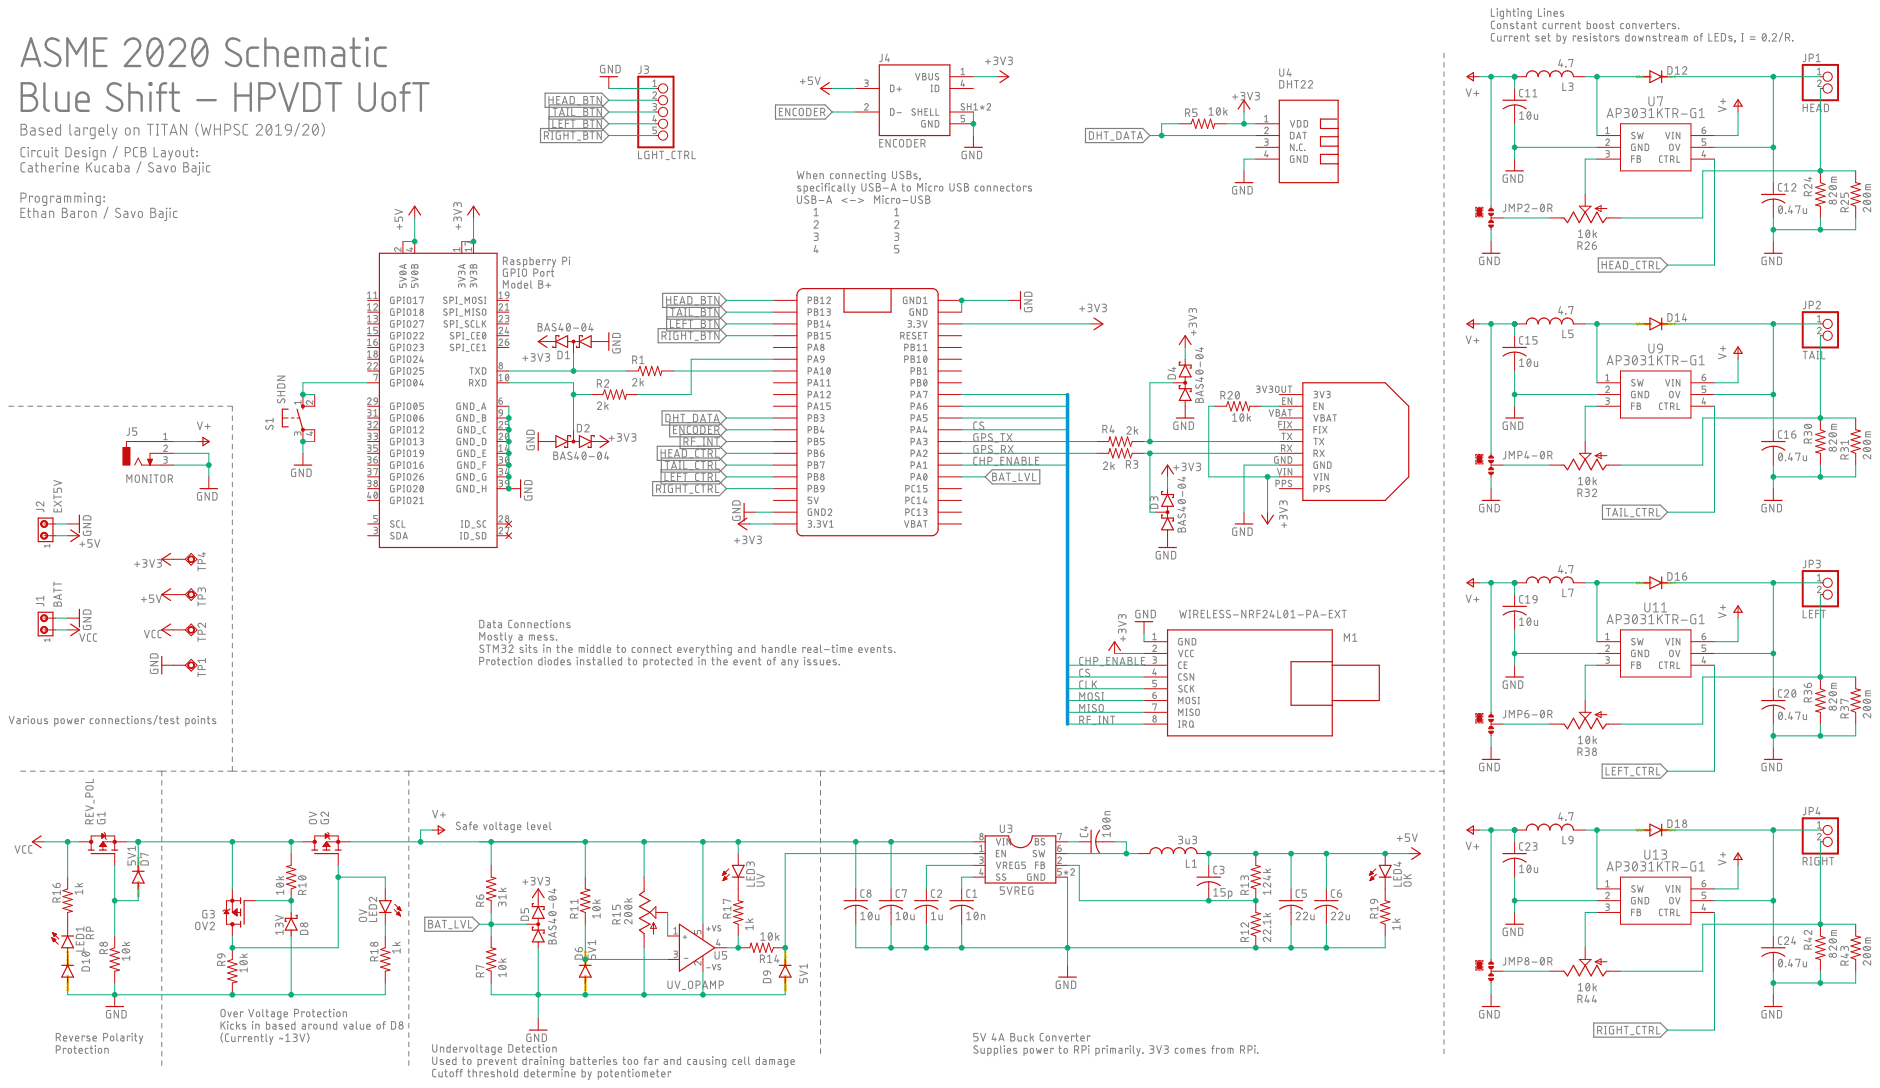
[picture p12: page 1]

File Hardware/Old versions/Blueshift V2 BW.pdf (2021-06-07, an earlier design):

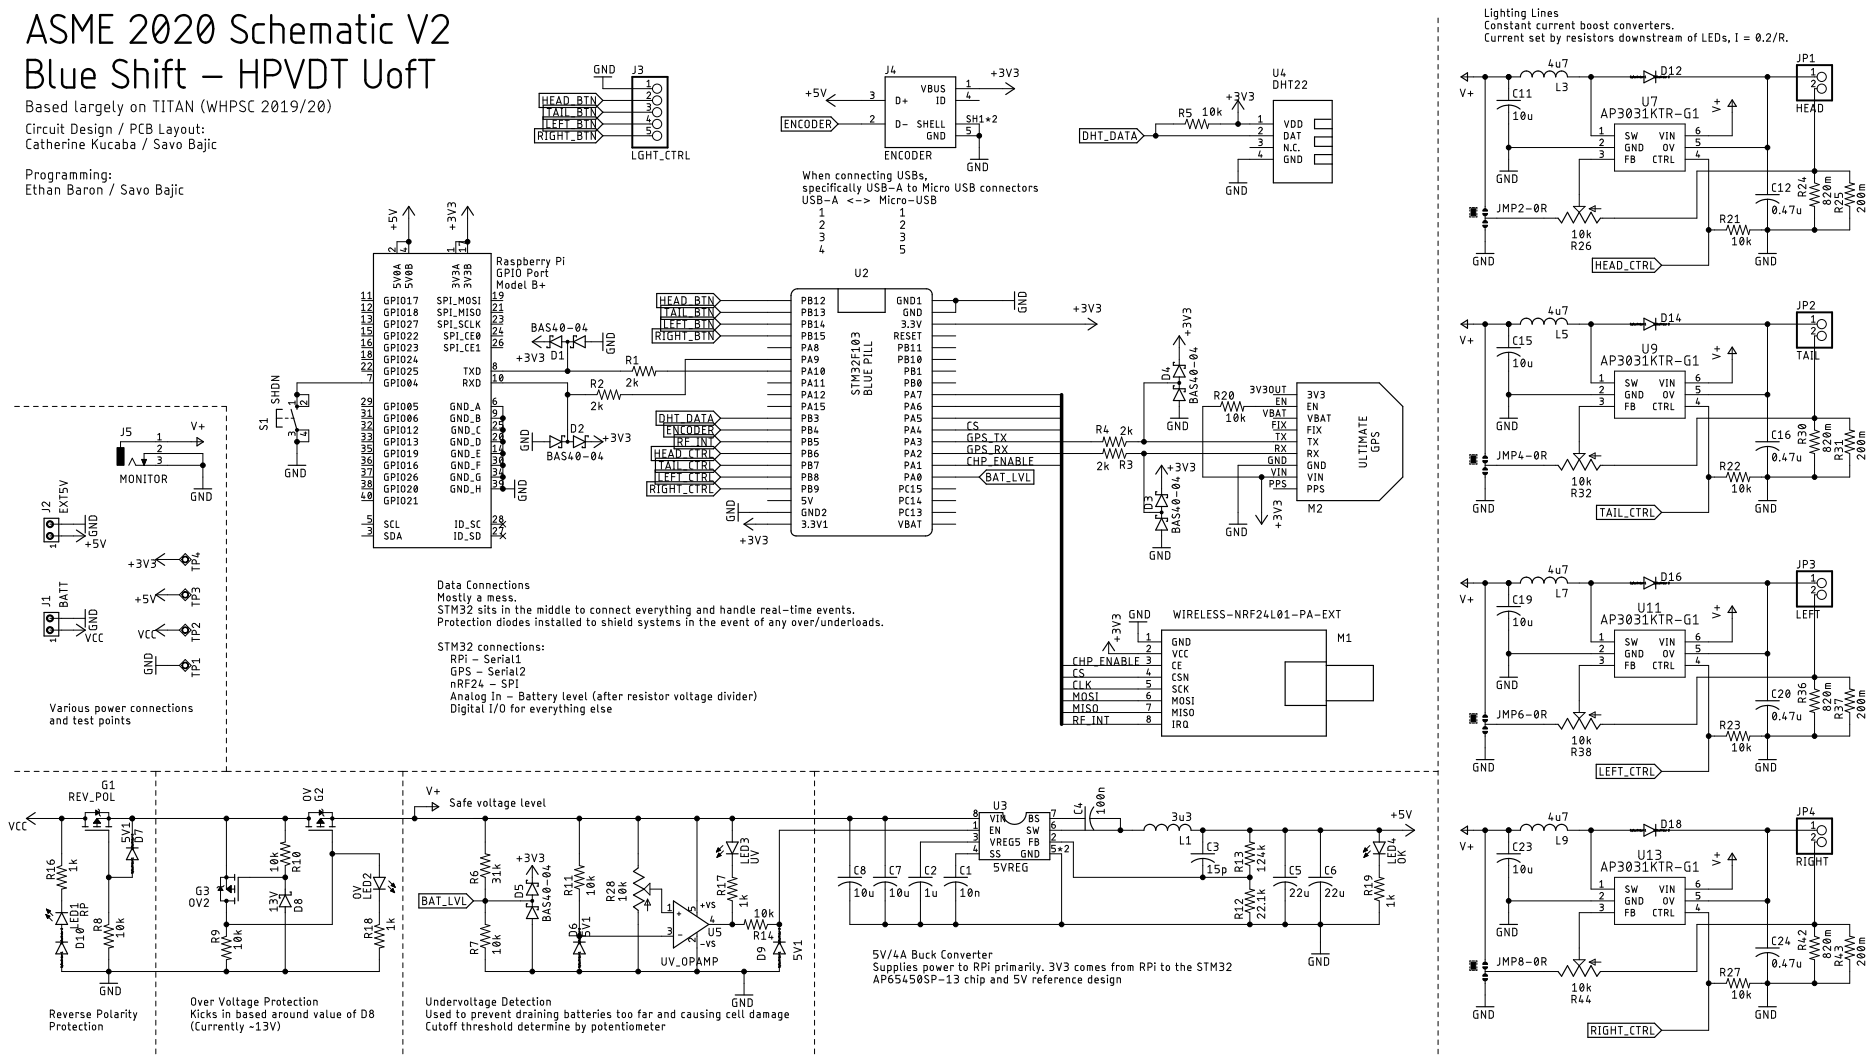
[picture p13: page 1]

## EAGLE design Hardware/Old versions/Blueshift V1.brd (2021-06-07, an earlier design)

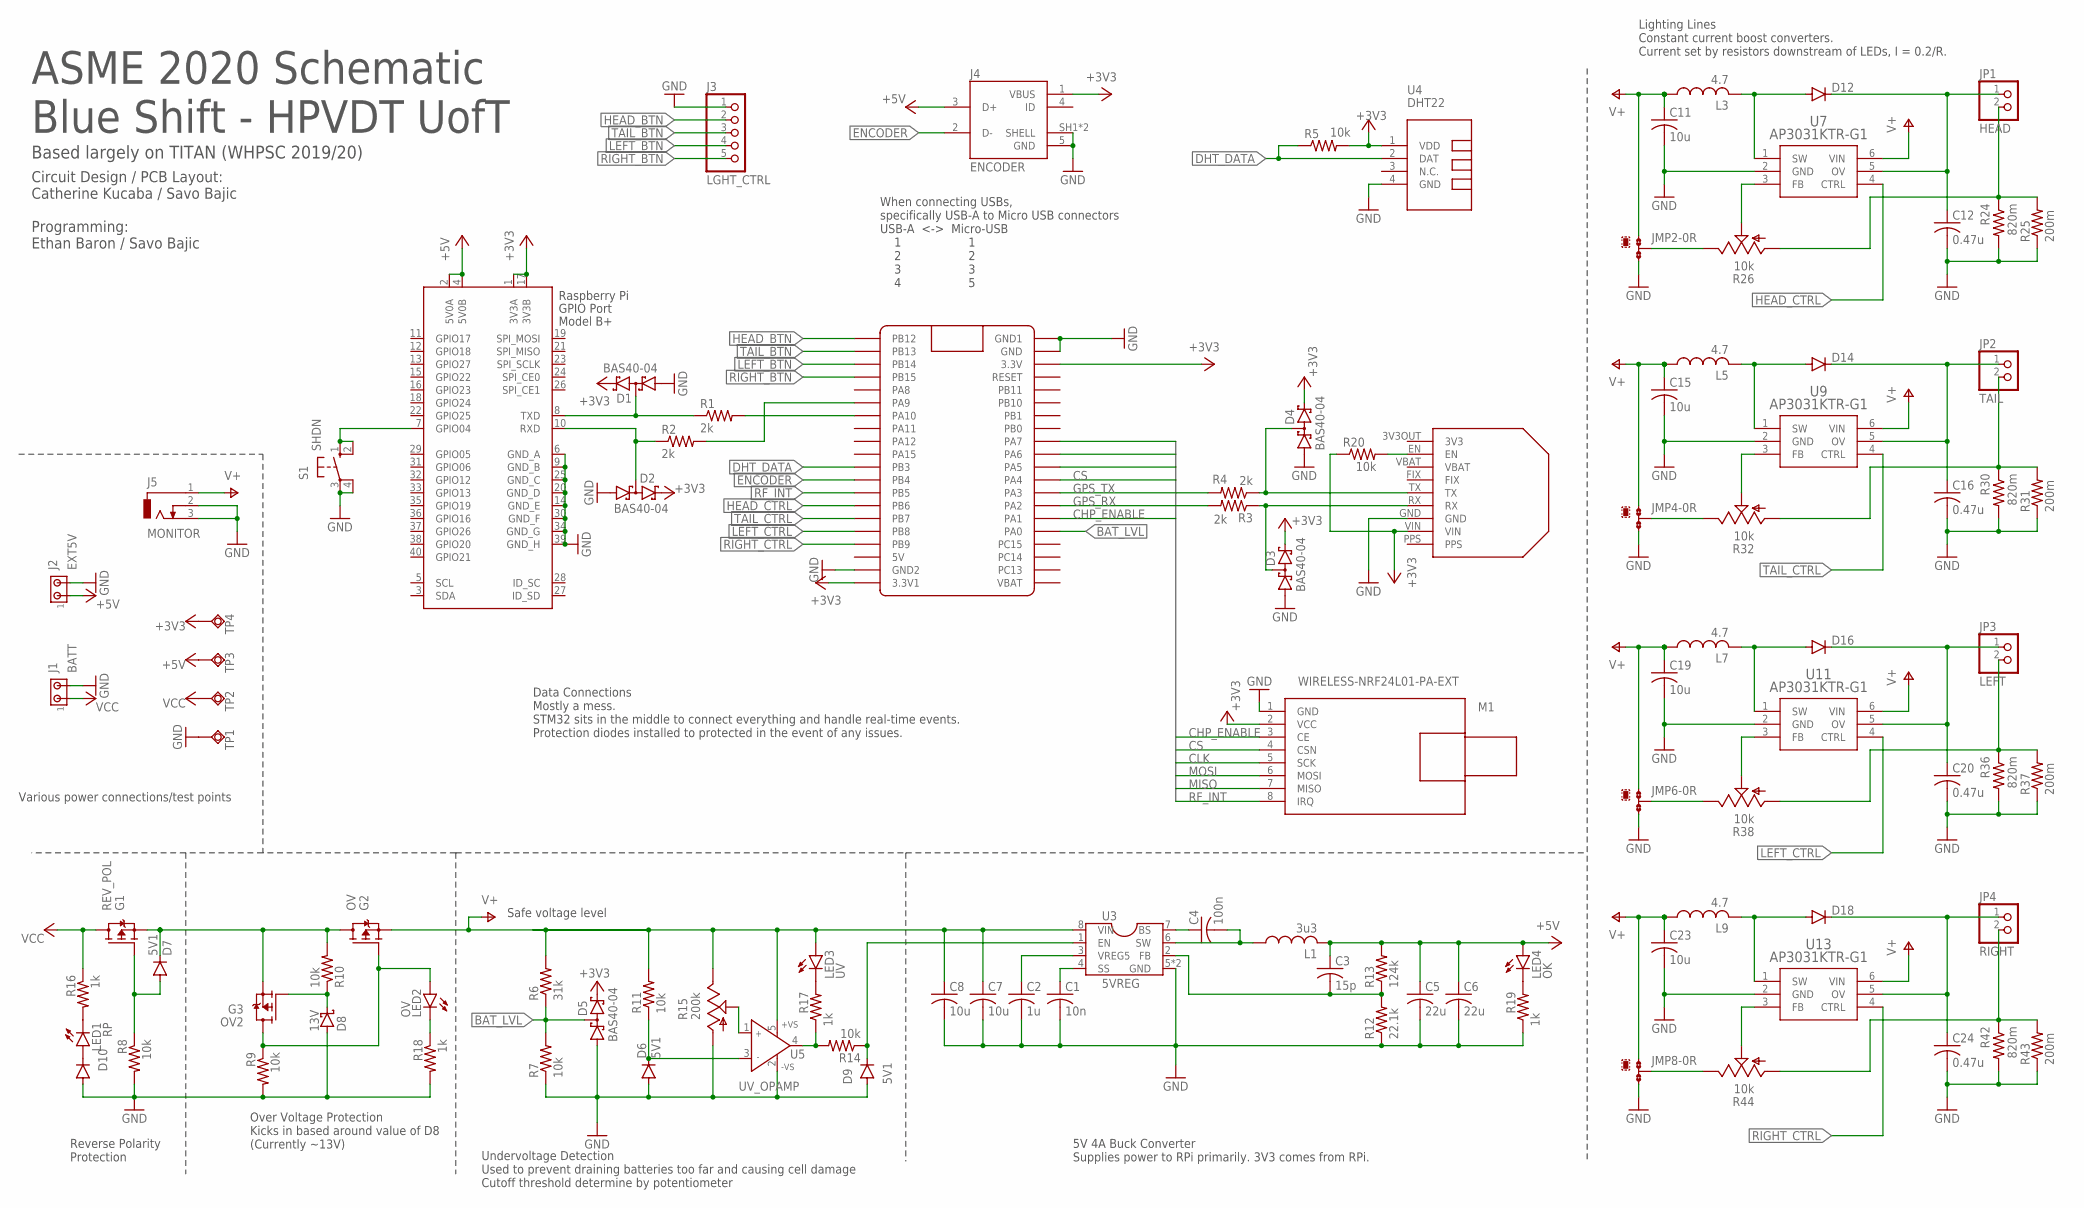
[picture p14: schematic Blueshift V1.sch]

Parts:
C1: 10n; C0402
C2: 1u; C0402
C3: 15p; C0402
C4: 100n; C0402
C5, C6: 22u; C0805
C7, C8: 10u; C0805
C11, C15, C19, C23: 10u; C1206K
C12, C16, C20, C24: 0.47u; C1206K
D1, D2, D3, D4, D5: BAS40-04; SOT23
D6, D7, D9: 5V1; SOD323-R
D8: 13V; SOT23
D10: DIODE-SOD80C; SOD80C
D12, D14, D16, D18: DIODE-DO-214AC; DO-214AC
G1: REV_POL; TSOP-6
G2: OV; TSOP-6
G3: OV2; TSOP-6
J1: BATT; 1X2MTA
J2: EXT5V; 1X2MTA
J3: LGHT_CTRL; 1X05
J4: ENCODER; TE_2172034-1
J5: MONITOR; DCJ0303
JMP2, JMP4, JMP6, JMP8: 0R-JUMPA; A0R-JMP
JP1: HEAD; 1X02
JP2: TAIL; 1X02
JP3: LEFT; 1X02
JP4: RIGHT; 1X02
L1: 3u3; SDES064T
L3, L5, L7, L9: 4.7; INDDFN600X600X280-2N
LED1: RP; SML0805
LED2: OV; SML0805
LED3: UV; SML0805
LED4: OK; SML0805
M1: WIRELESS-NRF24L01-PA-EXT
M2: ULTIMATE-GPS; ULTIMATE_GPS
R1, R2, R3, R4: 2k; R0402
R5, R7, R8, R9, R10, R11, R14, R20: 10k; R0402
R6: 31k; R0402
R12: 22.1k; R0402
R13: 124k; R0402
R15: 200k; CA6V
R16, R17, R18, R19: 1k; R0402
R24, R30, R36, R42: 820m; R0603
R25, R31, R37, R43: 200m; R0805
R26, R32, R38, R44: 10k; RJ9W
S1: SHDN; B3F-10XX
TP1: TPSQTP20SQ; TP20SQ
TP2, TP3, TP4: TPSQTP20R; TP20R
U1: RASPI_HAT; RASPI_BOARD_B+HAT_CF
U2: BLUEPILL; BLUE_PILL
U3: 5VREG; SO-8EP
U4: DHT22; TEMP-HUM-SENSOR-DHT22
U5: UV_OPAMP; SOT-753
U7, U9, U11, U13: AP3031KTR-G1; SOT23-6

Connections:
5V_FB: C3.2, R12.2, R13.1, U3.2 (FB)
+3V3: D1.2 (C2), D2.2 (C2), D3.2 (C2), D4.2 (C2), D5.2 (C2), J4.1 (VBUS), M1.2 (VCC), M2.VIN, R5.2, R20.1, TP4.TP, U1.1 (3V3A), U1.17 (3V3B), U2.P$20 (3.3V1), U2.P$23 (3.3V), U4.1 (VDD)
+5V: C3.1, C5.1, C6.1, J2.1, J4.3 (D+), L1.2, LED4.A, R13.2, TP3.TP, U1.2 (5V0A), U1.4 (5V0B)
BAT_LVL: D5.3 (C1A2), R6.1, R7.2, U2.P$36 (PA0)
CHP_ENABLE: M1.3 (CE), U2.P$35 (PA1)
CLK: M1.5 (SCK), U2.P$31 (PA5)
CS: M1.4 (CSN), U2.P$32 (PA4)
DHT_DATA: R5.1, U2.P$11 (PB3), U4.2 (DAT)
ENCODER: J4.2 (D-), U2.P$12 (PB4)
GND: C1.2, C2.2, C5.2, C6.2, C7.2, C8.2, C11.2, C12.2, C15.2, C16.2, C19.2, C20.2, C23.2, C24.2, D1.1 (A1), D2.1 (A1), D3.1 (A1), D4.1 (A1), D5.1 (A1), D6.A, D8.1 (A), D9.A, D10.A, J1.2, J2.2, J3.1, J4.5 (GND), J4.SH1 (SHELL), J4.SH2 (SHELL), J5.2, J5.3, JMP2.3, JMP4.3, JMP6.3, JMP8.3, M1.1 (GND), M2.GND, R7.1, R8.2, R9.2, R12.1, R15.A, R18.2, R19.1, R24.2, R25.1, R30.2, R31.1, R36.2, R37.1, R42.2, R43.1, S1.3, S1.4 (P1), TP1.TP, U1.6 (GND_A), U1.9 (GND_B), U1.14 (GND_E), U1.20 (GND_D), U1.25 (GND_C), U1.30 (GND_F), U1.34 (GND_G), U1.39 (GND_H), U2.P$19 (GND2), U2.P$21 (GND1), U2.P$22 (GND), U3.5 (GND), U3.TP (GND), U4.4 (GND), U5.2 (-VS), U7.2 (GND), U9.2 (GND), U11.2 (GND), U13.2 (GND)
GPS_RX: R3.2, U2.P$34 (PA2)
GPS_TX: R4.2, U2.P$33 (PA3)
HEAD_BTN: J3.2, U2.P$1 (PB12)
HEAD_CTRL: U2.P$14 (PB6), U7.4 (CTRL)
LEFT_BTN: J3.4, U2.P$3 (PB14)
LEFT_CTRL: U2.P$16 (PB8), U11.4 (CTRL)
MISO: M1.7 (MISO), U2.P$30 (PA6)
MOSI: M1.6 (MOSI), U2.P$29 (PA7)
unnamed: R1.2, U2.P$7 (PA10)
unnamed: R2.2, U2.P$6 (PA9)
unnamed: D1.3 (C1A2), R1.1, U1.8 (TXD)
unnamed: D2.3 (C1A2), R2.1, U1.10 (RXD)
unnamed: D3.3 (C1A2), M2.RX, R3.1
unnamed: S1.1 (S), S1.2 (S1), U1.7 (GPIO04)
unnamed: D8.3 (C), G3.3 (G), R10.1
unnamed: D7.A, G1.3 (G), R8.1
unnamed: D4.3 (C1A2), M2.TX, R4.1
unnamed: G2.3 (G), G3.1 (D), G3.2 (D), G3.5 (D), G3.6 (D), LED2.A, R9.1
unnamed: LED3.C, R17.2
unnamed: C1.1, U3.4 (SS)
unnamed: D6.C, R11.1, U5.3 (IN-)
unnamed: C4.2, L1.1, U3.6 (SW)
unnamed: C2.1, U3.3 (VREG5)
unnamed: C4.1, U3.7 (BS)
unnamed: R14.2, R17.1, U5.4 (OUT)
unnamed: D9.C, R14.1, U3.1 (EN)
unnamed: R15.S, U5.1 (IN+)
unnamed: LED1.C, R16.2
unnamed: D10.C, LED1.A
unnamed: M2.EN, R20.2
unnamed: LED2.C, R18.1
unnamed: LED4.C, R19.2
unnamed: D7.C, G1.4 (S), G2.1 (D), G2.2 (D), G2.5 (D), G2.6 (D), G3.4 (S), R10.2
unnamed: D12.A, L3.2, U7.1 (SW)
unnamed: JMP2.2, R26.E
unnamed: R26.S, U7.3 (FB)
unnamed: C12.1, D12.C, JP1.1, U7.5 (OV)
unnamed: JP1.2, R24.1, R25.2, R26.A
unnamed: D14.A, L5.2, U9.1 (SW)
unnamed: JMP4.2, R32.E
unnamed: R32.S, U9.3 (FB)
unnamed: C16.1, D14.C, JP2.1, U9.5 (OV)
unnamed: JP2.2, R30.1, R31.2, R32.A
unnamed: D16.A, L7.2, U11.1 (SW)
unnamed: JMP6.2, R38.E
unnamed: R38.S, U11.3 (FB)
unnamed: C20.1, D16.C, JP3.1, U11.5 (OV)
unnamed: JP3.2, R36.1, R37.2, R38.A
unnamed: D18.A, L9.2, U13.1 (SW)
unnamed: JMP8.2, R44.E
unnamed: R44.S, U13.3 (FB)
unnamed: C24.1, D18.C, JP4.1, U13.5 (OV)
unnamed: JP4.2, R42.1, R43.2, R44.A
RF_INT: M1.8 (IRQ), U2.P$13 (PB5)
RIGHT_BTN: J3.5, U2.P$4 (PB15)
RIGHT_CTRL: U2.P$17 (PB9), U13.4 (CTRL)
TAIL_BTN: J3.3, U2.P$2 (PB13)
TAIL_CTRL: U2.P$15 (PB7), U9.4 (CTRL)
V+: C7.1, C8.1, C11.1, C15.1, C19.1, C23.1, G2.4 (S), J5.1, JMP2.1, JMP4.1, JMP6.1, JMP8.1, L3.1, L5.1, L7.1, L9.1, LED3.A, R6.2, R11.2, R15.E, U3.8 (VIN), U5.5 (+VS), U7.6 (VIN), U9.6 (VIN), U11.6 (VIN), U13.6 (VIN)
VCC: G1.1 (D), G1.2 (D), G1.5 (D), G1.6 (D), J1.1, R16.1, TP2.TP

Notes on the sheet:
When connecting USBs, specifically USB-A to Micro USB connectors USB-A <-> Micro-USB 1 1 2 2 3 3 4 5
Safe voltage level
Various power connections/test points
Undervoltage Detection Used to prevent draining batteries too far and causing cell damage Cutoff threshold determine by potentiometer
5V 4A Buck Converter Supplies power to RPi primarily. 3V3 comes from RPi.
Lighting Lines Constant current boost converters. Current set by resistors downstream of LEDs, I = 0.2/R.
Data Connections Mostly a mess. STM32 sits in the middle to connect everything and handle real-time events. Protection diodes installed to protected in the event of any issues.
Reverse Polarity Protection
Over Voltage Protection Kicks in based around value of D8 (Currently ~13V)
ASME 2020 Schematic Blue Shift - HPVDT UofT
Based largely on TITAN (WHPSC 2019/20)
Circuit Design / PCB Layout: Catherine Kucaba / Savo Bajic Programming: Ethan Baron / Savo Bajic

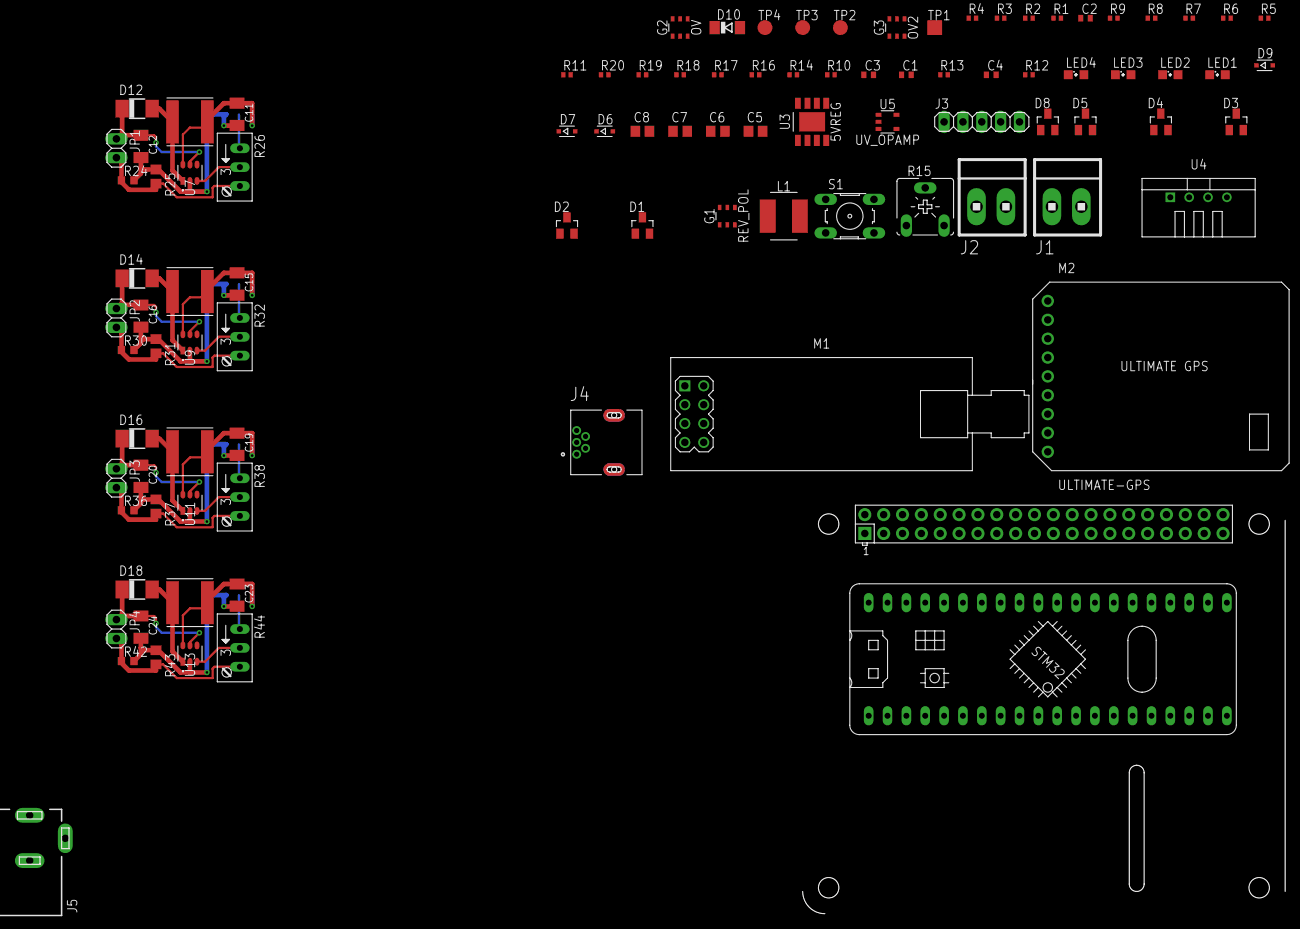
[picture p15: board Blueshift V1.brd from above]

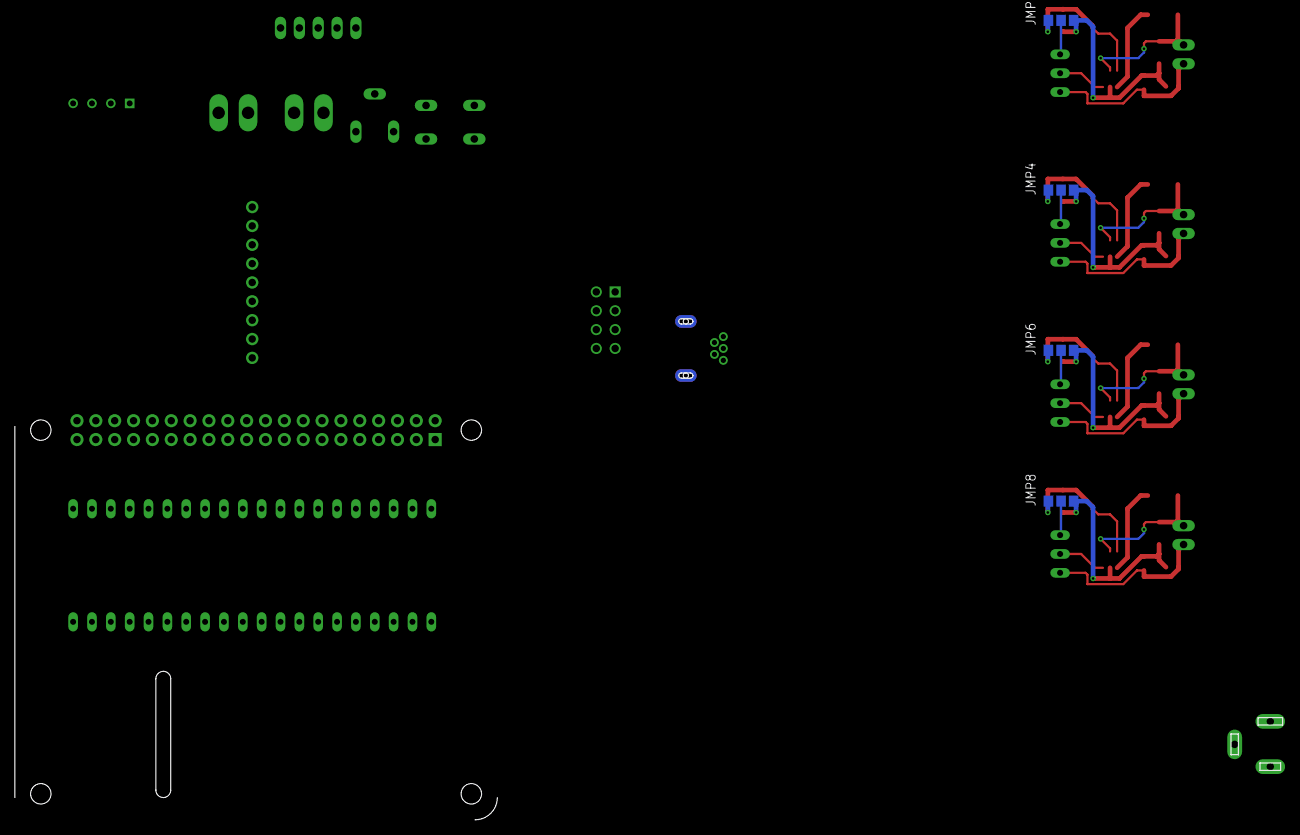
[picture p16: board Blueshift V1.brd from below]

Board: 2 copper layers, 103 parts (4 on the bottom side), 70 nets.

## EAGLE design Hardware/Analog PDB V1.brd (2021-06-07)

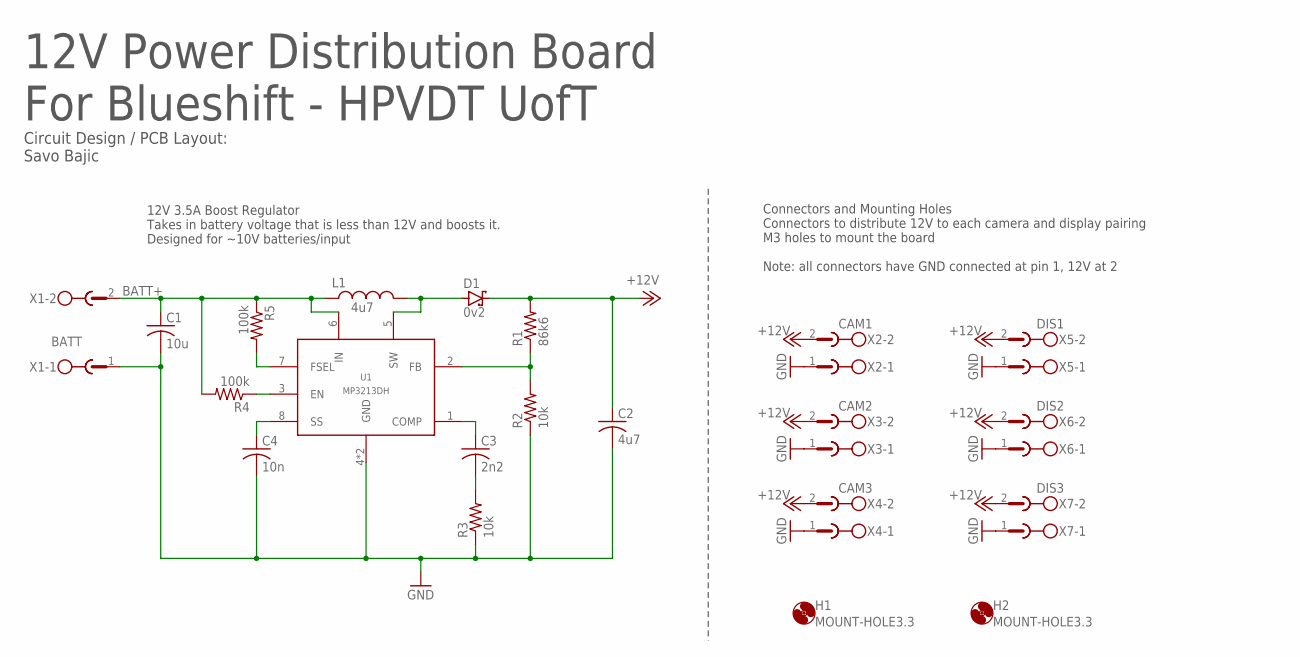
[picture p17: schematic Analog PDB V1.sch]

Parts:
C1: 10u; C0603
C2: 4u7; C0603
C3: 2n2; C0603
C4: 10n; C0603
D1: 0v2; DO-214AB
H1, H2: MOUNT-HOLE3.3; 3,3
L1: 4u7; SDES053T
R1: 86k6; R0402
R2, R3: 10k; R0402
R4, R5: 100k; R0402
U1: MP3213DH; 8-TSSOP
X1: BATT; MSTBV2
X2: CAM1; MSTBV2
X3: CAM2; MSTBV2
X4: CAM3; MSTBV2
X5: DIS1; MSTBV2
X6: DIS2; MSTBV2
X7: DIS3; MSTBV2

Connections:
+12V: C2.1, D1.C, R1.2, X2.2, X3.2, X4.2, X5.2, X6.2, X7.2
BATT+: C1.1, L1.1, R4.2, R5.1, U1.6 (IN), X1.2
EN: R4.1, U1.3 (EN)
FEEDBACK: R1.1, R2.2, U1.2 (FB)
FREQSELECT: R5.2, U1.7 (FSEL)
GND: C1.2, C2.2, C4.2, R2.1, R3.1, U1.4 (GND), U1.P (GND), X1.1, X2.1, X3.1, X4.1, X5.1, X6.1, X7.1
unnamed: D1.A, L1.2, U1.5 (SW)
unnamed: C3.1, U1.1 (COMP)
unnamed: C3.2, R3.2
SOFTSTART: C4.1, U1.8 (SS)

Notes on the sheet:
12V 3.5A Boost Regulator Takes in battery voltage that is less than 12V and boosts it. Designed for ~10V batteries/input
Connectors and Mounting Holes Connectors to distribute 12V to each camera and display pairing M3 holes to mount the board Note: all connectors have GND connected at pin 1, 12V at 2
12V Power Distribution Board For Blueshift - HPVDT UofT
Circuit Design / PCB Layout: Savo Bajic

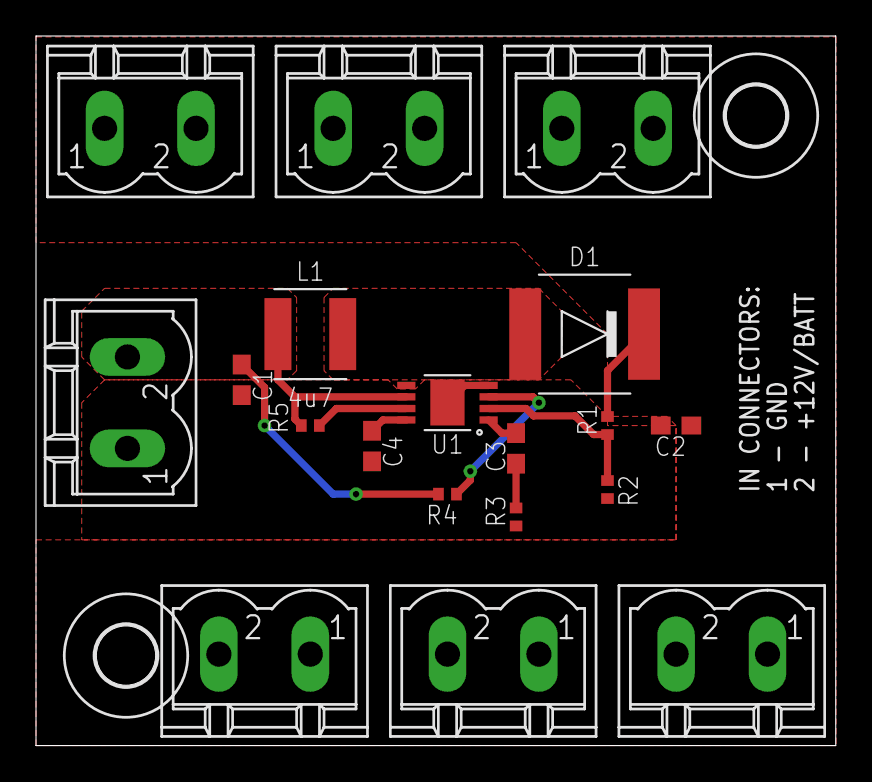
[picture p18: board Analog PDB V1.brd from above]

Board: 2 copper layers, 44.4 x 39.4 mm, 21 parts (0 on the bottom side), 10 nets.

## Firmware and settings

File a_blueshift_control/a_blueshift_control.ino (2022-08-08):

#include <TinyGPS.h>
#include "DHT.h" // Used for temperature and humidity

#define FRONTSERIAL Serial1
#define GPSSERIAL Serial2
#define DEBUGSERIAL Serial
/* Serial Pins
   PA9 - TX1
   PA10 - RX1

   PA2 - TX2
   PA3 - RX2

   PB10 - TX3
   PB11 - RX3
*/

// DEBUGGING MODE
bool debugMode = false;      // In debug mode or not (copies all messages to debug serial line

const long rpiBaud = 115200;  // Baudrate used with rpis
const long gpsBaud = 9600;    // Baudrate used with GPS
const long debugBaud = 115200;  // Baudrate for debugging line

/////////////////////////////////////////////////
// Variables
int FHR = 10;               // Front heart rate (BPM)
int RHR = 10;               // Rear heart rate
int FCadence = 10;          // Cadence (RPM)
int RCadence = 10;
int FPower = 10;            // Power (W)
int RPower = 10;

int FBatt = 100;            // Front battery %
int RBatt = 100;            // Rear battery %
int SBatt = 100;            // Spare battery %

byte humidity = 0;          // Humidity
byte temperature = 50;      // Temperature

volatile float speedKm = 0; // Speed (km/h)
volatile unsigned int rotationCount = 0; // Number of complete wheel roations

float latitude = 0;         // Latitude (degrees)
float longitude = 0;        // Longitude (degrees)
float altitudeGPS = 0;      // Altitude (m)
float speedGPS = 0;         // GPS speed in km/h
float distanceGPS = 0;      // GPS distance in km
// Coordinates that mark the start point (used for getting distance by GPS) 
float startLong = -117.043375;
float startLat = 40.393598;

byte testY = 0;             // Used solely for echo tests
byte testZ = 0;             // Used solely for echo tests

//////////////////////////////////////////////////
// Pin allocation
const byte DHTPin = PB3;  // DHT sensor pin (temperature and humidity)
const byte FBPin = PA0;   // Front battery pin (ADC)
const byte SBPin = PB0;   // Spare battery pin (ADC)
const byte encoderPin = PB4;   // Encoder interrupt pin

// Digital Humidity and Temperature setup
DHT dht(DHTPin, DHT22); // Sets up sensor
const unsigned int dhtPeriod = 500; // Period between measurements
unsigned long dhtTime = 0; // Stores next time to take measurement

// GPS Module
TinyGPS gps;

// Battery monitoring period
const unsigned long batteryPeriod = 2000; // Battery check period (every few seconds)
unsigned long batteryTime = 0;  // Stores time for next battery check

// Wheel monitoring parameters
const byte numberTicks = 6; // Number of ticks per complete rotation of wheel
volatile byte currentTick = 0; // Stores which tick we are on
volatile byte previousTick = numberTicks; // Stores what tick we were previously on

const float periodToKMH = 7495200; // Divide this by period in microseconds to get speed in km/h
// periodToKM is determined by multiplying circumference in meters by 3.6 x 10^6
volatile unsigned long lastPass[numberTicks]; // Stores the last trigger time for each tick
const unsigned long debounce = 4000; // Debounce period in us. Prevents there being repeated measurements from flickering

unsigned long wheelTime = 0; // Check if wheel has timed out (stopped)
const unsigned int wheelTimeout = 500; // Timeout period
float previousSpeed = 0; // Stores speed for comparison

////////////////////////////////////////////////////////////////
// Telemetry related declarations
#include <RF24-STM.h>

const byte radioInteruptPin = PB5;
const byte radioCSPin = PA4;
const byte radioEnablePin = PA1;

// Hardware configuration: Set up nRF24L01 radio on SPI bus plus pins 7 & 8
RF24 radio(radioEnablePin, radioCSPin);
bool recieverRole = true; // Are we the reciever? Vehicle is 'reciever', station is 'sender'

// Communication pipes to use
const uint64_t pipes[2] = { 0x1122334471LL, 0x112233447CLL };

volatile bool recievedRadioData = false; // Used to record a recieve event
char radioMessage[32]; // Buffer for message (nRF24 messages are limited to 32 bytes each)
byte pipeNumber; // Stores the origin of the message (used in reciever mode)









void setup() {
  // Pin modes,
  // !!! verify if encode pin is meant to be pull up or down!!!!!
  pinMode(LED_BUILTIN, OUTPUT); // Used for status indicator
  pinMode(FBPin, INPUT_ANALOG); // Battery pins
  pinMode(SBPin, INPUT_ANALOG);
  pinMode(encoderPin, INPUT_PULLUP); // Encoder interupt

  attachInterrupt(encoderPin, encoderDetect, RISING); // Encoder interupt
  // !!! VERIFY IF FALLING OR RISING !!!

  // Start each serial line
  FRONTSERIAL.begin(rpiBaud);
  GPSSERIAL.begin(gpsBaud);
  DEBUGSERIAL.begin(debugBaud);

  blinker(1500, 5); // Start-up blinking, gives delay for debugging to connect
  
  // Debug timeout
  const int timeout = 2000; // Time out for debugger to be started if debugging
  unsigned long endTime = millis() + timeout; // End time for scanning

  if (debugMode) {
    // Set up debugging mode (USB connection)

    while (!DEBUGSERIAL) {
      delay(100); // wait for serial port to connect. Needed for native USB

      if (millis() > endTime) {
        // Once timeout has been reached
        debugMode = false; // Disable debugging
        break; // Exit loop
      }
    }

    if (debugMode) {
      DEBUGSERIAL.println(F("DEBUGGING MODE")); // Print debug statement if no timeout
      blinker(600, 3);
    }
  }

  // Sensor setup
  dht.begin(); // Starts digital humidity and temperature sensor

  for (byte i = 0; i < numberTicks; i++) {
    lastPass[i] = 0; // Reset all encoder tick values
  }

  setupRadio(); // Set up radio
  
  blinker(100, 10); // Blink a few times on successful startup
}

void loop() {
  if (FRONTSERIAL.available()) {
    // Data on front line
    processData('f');
  }
  if (DEBUGSERIAL.available()) {
    // Data on debugging line
    processData('d');
  }

  // Periodic DHT measurement
  if (millis() > dhtTime) {
    humidity = dht.readHumidity() * 2;            // Humidity reading
    temperature = 50 + (dht.readTemperature() * 2); // Temperature reading

    dhtTime = millis() + dhtPeriod; // Sets next measurement time
  }

  // Periodic battery check
  if (millis() > batteryTime) {
    FBatt = batteryLevel('f');
    SBatt = batteryLevel('s');

    batteryTime = millis() + batteryPeriod; // Sets next check
  }

  // Periodic speed check
  if (millis() > wheelTime) {
    if (speedKm == previousSpeed) speedKm = 0; // Reset speed if no change

    previousSpeed = speedKm; // Updates speed
    wheelTime = millis() + wheelTimeout; // Sets next check
  }

  /////////////////////////////////////////
  // GPS code
  if (GPSSERIAL.available()) {
    GPSCheck();
  }

  //////////////////////////////////////////
  // Telemetry Code
  if (recievedRadioData) {
    recievedRadioData = false; // Clear flag
    radioRecieved();
    processData('t');
  }
  delayMicroseconds(10); // Regular delay
}

void blinker (const int period, const byte repeats) {
  // Blink LED a number of times for a given length
  for (byte i = 0; i < repeats; i++) {
    digitalWrite(LED_BUILTIN, LOW);
    delay(period / 2);
    digitalWrite(LED_BUILTIN, HIGH);
    delay(period / 2);
  }
  // Note on STM32 LED is on when pin is LOW!
}

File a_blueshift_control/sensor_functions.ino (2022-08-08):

byte batteryLevel (char line) {
  // Factor by which to divide ADC reading (4095 at max, 3.3 ref)
  // Also need to voltage account for voltage division
  // Also need record each STM32's '3.3V' rail actual voltage
  const float readingToV = 1241.2121; // Given by 4096 over measured voltage
  const float fFactor = 4.3739; // Resistor voltage division factor
  const float rFactor = 4.3087;
  const float sFactor = 4.3072;

  // Get the voltage on whichever line
  float reading = 0.0;
  switch (line) {
    case 'f':
      reading = float(analogRead(FBPin));
      reading /= readingToV;
      reading *= fFactor;
      break;
    case 's':
      reading = float(analogRead(SBPin));
      reading /= readingToV;
      reading *= sFactor;
      break;
  }

  /* Convert voltage to % according to battery properties

    Uses linear interpolation to determine battery percentage.
    Starts from second highest set point (99%) and sees if the
    reading is higher than the set point. If it is, it'll
    interpolate using the set point and the next higher one.
    If the reading is less than the set point move to the next
    interval and repeat

    Voltages and percentages were sourced from:
    https://www.solacity.com/how-to-keep-lifepo4-lithium-ion-batteries-happy/
    And adjusted from 4 cells to 3 (by multiplying voltages by 0.75)
  */
  if (reading > 0) {
    const byte level[] = {100, 99, 90, 70, 40, 30, 20, 17, 14, 9, 0}; // Percentages linked to voltages
    const float voltage[] = {10.2, 10.05, 9.975, 9.9, 9.825, 9.75, 9.675, 9.6, 9.375, 9, 7.5}; // Voltages

    // Run though set point from
    for (byte i = 1; i <= 11; i++) {
      if (reading > voltage[i]) {
        // If the reading is in the region
        float temp = 0; // Used in calculations

        // Linear interpolation formula
        temp = (reading - voltage[i]) * float(level[i - 1] - level[i]);
        temp /= float(voltage[i - 1] - voltage[i]);
        temp += level[i];

        reading = temp; // Stores the result in the reading variable
        break;
      }
    }
  }
  reading = constrain(reading, 0, 100); // Constrain it to reasonable values

  return (int(reading));
}

void encoderDetect () {
  const unsigned long triggerTime = micros(); // Use micros instead of millis for higher precision

  if (triggerTime > (lastPass[previousTick] + debounce)) {
    // Checks if we have passed the debounce period from the last measurement

    speedKm = periodToKMH / (triggerTime - lastPass[currentTick]); // Gets speed from period
    lastPass[currentTick] = triggerTime; // Update trigger time for next run

    previousTick = currentTick; // Marks the current tick as the previous one for the next call
    // Using this variable reduces tha=e calculations that occur when this routine is called

    // Updates tick indexes, cycling around when at the end
    if (currentTick == numberTicks - 1) {
      currentTick = 0;
      rotationCount++; // Increases rotation count with each full cycle
    }
    else currentTick++;
  }
}

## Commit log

2020-03-06 Initial commit
    Basically all the TITAN code but with the extra files trimmed out and some renamed to reference Blueshift to avoid confusion
    [buildout.cfg]
2021-06-07 Uploaded hardware files
    [Analog PDB Part BOM.csv, Analog PDB V1.brd, Analog PDB V1.sch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]
2022-08-08 Changed code to reflect a lack of other boards in Blueshift

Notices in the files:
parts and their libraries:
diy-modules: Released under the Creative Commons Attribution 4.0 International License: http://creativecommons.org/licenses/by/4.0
